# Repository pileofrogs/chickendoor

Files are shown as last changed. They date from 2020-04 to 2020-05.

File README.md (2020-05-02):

# chickendoor

We have chickens and live near Seattle where dawn is very early in the summers.
A system that opens the door to the chicken coop automatically means we can sleep in.  If it can also close the door, it makes vacations easier for a pet sitter.  

## Requirements

* Must fail safe:  IE if it breaks down, we can still open the door and latch it at night. - This is acheived by having the actuator outside of the chicken house and attached with simple pins that a person can pull out without tools
* Must be racoon proof:  Or you might as well not have a door
* Must not crush chickens:  This probably rarely happens, but I would feel aweful if it did.  I added a pressure sensor to make the door open if it hits anything.  
* Open and close based on sunrise & sunset:  No manual adjustmenst over the year.

## Files 

* openscad files for project box, pressure sensor & bracket
* openscad files for helpful objects (screw hole sizer, rpi mount position test)
* python code for running on Rpi

Requires a linear actuator, a set of 2 12v relays, a 12 & 5 v power supply, 
2 buttons && whatever I'm not remembering.

## How it works

The actuator is anchored on the wall outside of the door and to the door, so
when it retracts, it opens the door.  The pressure sensor is basically a hinge
connecting the actuator to the door with a button inside it.  When the actuator
presses on the hinge, it applies pressure to the button.  I just need to
position the button and possibly apply opposing elasic force.  

## TODO

* retry closing if we hit a chicken
* poweroff with long press
* log to syslog/journal
* send alerts if it hits a chicken or has other problems

## For version III

* config file for time offsets
* make brackets adjustable
* make it a service that I can interact with using a client
* make separate monitoring system that can send alerts if the chicken door opener dies
* figure out math for positioning the actuator
* separate latching mechanism
* camera and imge processing to count chickens
* anit-hawk rail-gun with tracking and flight prediction

## Lessons Leaned

* The slop between the pins and the holes they go through really matters.  Shutting the door firmly wihtout setting off the pressure sensor depends on minimal slop.  I was able to offset this by cramming some wire into the holes and screwing wood to the door, making it thicker.  
* setting one of the brackes a few inches off of the wall would really help.  As it is, the closed door is a straight line between them so there's very little leverage keeping it closed and that means any slop translates into a lot of wiggle in the door.
* gpiozero is amazing.  I could have written much simpler code if I'd known how   it works before I got started.

# pins I used

* LEDs 4,17 
* Relays 27,22
* Buttons 23,24

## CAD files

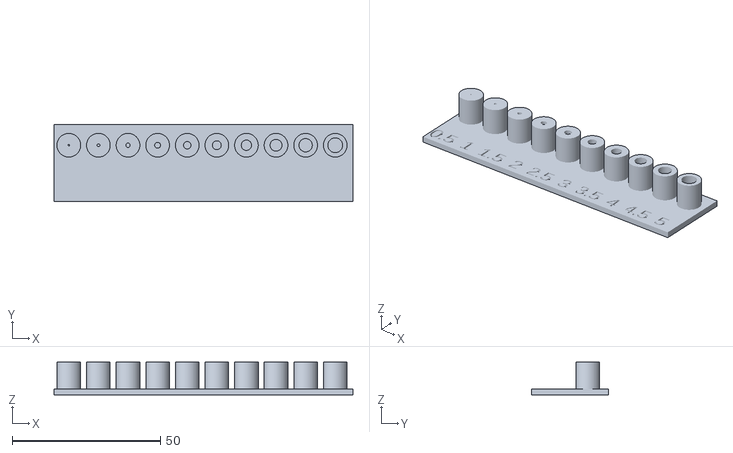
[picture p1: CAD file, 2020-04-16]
screw_hole_sizer.stl
101.0 x 26.0 x 11.0

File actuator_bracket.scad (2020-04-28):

act_r = 10.5;
act_hole_r = 3;
act_hole_d_to_end = 4;
act_hole_d_to_box = 8;
act_len = act_hole_d_to_end+act_hole_d_to_box+2*act_hole_r;
box = [39,39,39];
act_hole_shaft_len = 50;
clearance = 12; //
width = 5;
slop = 1;
upness = 30;

$fn = 100;

use <common_shapes.scad>;

echo(act_len);

module actuator () {
  hole_goes=act_hole_d_to_box+act_hole_r;
  translate([0,0,hole_goes]) rotate([0,90,0]) {
    translate([-box[0],-box[1]/2,-box[2]/2]) cube(box);
    difference() {
      rotate([0,90,0]) cylinder(act_len, act_r, act_r);
      translate([hole_goes, act_hole_shaft_len/2 , 0 ])
        rotate([90,0,0])
        cylinder( act_hole_shaft_len, act_hole_r, act_hole_r); 
    }
  }
}

module triangle (side,base) {
  hypot = sqrt(pow(side,2)+pow(base,2));
  angle = asin(base/hypot);
  difference () {
    cube([side,base,width]);
    translate([0,0,-1]) rotate([0,0,angle]) cube([hypot,base,width+2]);
  }
}

module ear () {
  translate ([0,0,clearance*2]) {
    rotate([-90,0,0]) {
      circler = act_hole_d_to_end+act_hole_r;
      difference () {
        union () {
          cylinder(width,circler,circler);
          translate([-circler,0,0]) cube([2*circler,2*clearance,width]);
          translate([-width/2,-circler+clearance,width]) 
            rotate([90,0,90])
            triangle(clearance+circler,clearance);
          translate([-circler,clearance,0]) rotate([0,0,90]) triangle(clearance,clearance/2);
          translate([circler,clearance,width]) rotate([180,0,90]) triangle(clearance,clearance/2);
        }
        translate([0,0,-1]) {
          cylinder(width+2,act_hole_r,act_hole_r);
        }
      }
    }
  }
}

translate([0,0,clearance*2]) %actuator();

translate([0,act_r+slop,0]) ear();
translate([0,-act_r-slop,0]) rotate([0,0,180])  ear();

ybase = 2*(clearance+width)+2*act_r+2*slop;
xbase = clearance+3*width;



difference() {
  translate([-xbase/2,-ybase/2,-width]) cube([xbase,ybase,width]);
  screw_head(3.5,4.1,2,width+slop);
  sx_offset = xbase/2-width;
  sy_offset = ybase/2-clearance/2;
  places = [
    [sx_offset,sy_offset,0],
    [-sx_offset,sy_offset,0],
    [sx_offset,-sy_offset,0],
    [-sx_offset,-sy_offset,0],
  ];
  for ( place = places ) {
    echo(place);
    translate(place) screw_head(3.5,4.1,2,width+slop);
  }
}

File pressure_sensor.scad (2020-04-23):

button = [6,3.5,3.5];

width = 5;
slop = 1;
pin_r = 2;

act_r = 10.5;
act_hole_r = 3;
act_len = 100;
act_hole_d_to_end = 6;
act_hole_shaft_len = 50;
hinge_plate_dims = [act_r*6, act_r*6, width];
barrel_r = width+pin_r;
wood_screw_radius = 2;
wood_screw_head_radius = 4.1;
wood_screw_head_height = 3.5;
wsr = wood_screw_radius;
wshr = wood_screw_head_radius;
wshh = wood_screw_head_height;

$fn = 100;

module actuator_piston () {
  hole_goes=-(act_hole_d_to_end+act_hole_r);
  %translate([hole_goes , 0, act_r]) {
    rotate([0,90,0]) cylinder(act_len, act_r, act_r);
    translate([-hole_goes, act_hole_shaft_len/2 , 0 ]) rotate([90,0,0]) cylinder( act_hole_shaft_len, act_hole_r, act_hole_r); 
  }
}

module ears ( thickness, rad, hole_rad ) {
  translate([0,rad,0]) difference() {
      union () {
          cylinder( thickness, rad, rad );
          translate([-rad*2,-rad,0]) cube([rad*4, rad, thickness]);
      }
      translate([0,0,-0.5]) cylinder( thickness+1, hole_rad, hole_rad);
      translate([ rad*2, 0, -0.5]) cylinder( thickness+1, rad,rad);
      translate([ -rad*2, 0, -0.5]) cylinder( thickness+1, rad,rad);
  }
}
translate([0,0,0.5*act_r]) actuator_piston();

module barrel_cut_out () {
    cylinder(hinge_plate_dims[0]/3+2*slop, barrel_r+slop, barrel_r+slop);
}

module hingetop () {
  // The flangy ear things around the piston
  translate([hinge_plate_dims[0]/2, hinge_plate_dims[1]/3-slop, 0]) rotate([90,0,0]) ears(width, 1.5 * act_r, act_hole_r);
  translate([hinge_plate_dims[0]/2, 2/3*hinge_plate_dims[1]+width+slop, 0]) rotate([90,0,0]) ears(width, 1.5 * act_r, act_hole_r);
  
  difference() {
    union () {
      // The hinge
      translate([0,0,-hinge_plate_dims[2]]) cube(hinge_plate_dims);
  
      // The barrel
      translate([hinge_plate_dims[0], 0, -barrel_r]) rotate([270, 0, 0]) 
      cylinder(hinge_plate_dims[0], barrel_r, barrel_r);
    }
    translate([hinge_plate_dims[0], 0, -barrel_r]) rotate([270, 0, 0]) {
      translate([0,0,-(slop/2)]) cylinder(hinge_plate_dims[0]+2,pin_r,pin_r);
      translate([0,0,-(slop/2)])  barrel_cut_out();
      translate([0,0, 2/3 * hinge_plate_dims[1]+slop])  barrel_cut_out();
    }
    // keeping it shut screw
    #translate([hinge_plate_dims[0]/6, hinge_plate_dims[1]/2, -wshh])
      screw_head();
  }

}

module hingebottom () {
  difference () {
    union () {
      translate([0,0, -hinge_plate_dims[2]]) cube(hinge_plate_dims);
      translate([0, 0, -barrel_r]) rotate([270, 0, 0]) 
        cylinder(hinge_plate_dims[0], barrel_r, barrel_r);
    }
    translate([0, 0, -barrel_r]) rotate([270, 0, 0]) {
      translate([0,0,-(slop/2)]) cylinder(hinge_plate_dims[0]+2,pin_r,pin_r);
      translate([0,0, hinge_plate_dims[1]/3+(slop/2)])  barrel_cut_out();
    }
    
    sixth = hinge_plate_dims[0]/6;
    screws_at = [ [barrel_r+sixth,sixth,0], 
                  [hinge_plate_dims[1]-sixth, sixth,0],
                  [hinge_plate_dims[1]-sixth, hinge_plate_dims[1]-sixth,0],
   		  [barrel_r+sixth,hinge_plate_dims[1]-sixth,0], 
    ];
    for ( screw_at = screws_at ) {
      translate(screw_at) rotate([180,0,0]) screw_head ();
    }
    // hole for keep-it-closed screw
    translate([hinge_plate_dims[0]-sixth, hinge_plate_dims[1]/2, -width-slop])
        cylinder(width+2*slop,wsr*1.5,wsr*1.5);
    // button trough
    trough_width = button[1]+2*slop;
    translate([-slop,hinge_plate_dims[1]/2-trough_width/2,-1.5*width])
      cube([hinge_plate_dims[0]+2*slop,button[1]+2*slop,width ]);
  }
}


translate([-hinge_plate_dims[0]/2,-hinge_plate_dims[1]/2,0]) hingetop();

translate([hinge_plate_dims[0]/2+barrel_r*2+2*slop,-hinge_plate_dims[1]/2,0]) hingebottom();

module screw_head () {
  overlap = wshh/100;
  translate([0,0,wshh-overlap]) cylinder(wshh,wshr,wshr);
  cylinder(wshh,wsr,wshr);
  translate([0,0,-wshh+slop]) cylinder(width+slop,wsr,wsr);
}

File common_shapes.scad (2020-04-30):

// wood_screw_head_height
// wood_screw_head_radius
// wood_screw_radius
// wood_screw_screw_height

module screw_head (wshh,wshr,wsr,wssh) {
  overlap = wshh/100;
  cylinder(1,wshr,wshr);
  translate([0,0,-wshh+overlap]) cylinder(wshh+overlap,wsr,wshr);
  translate([0,0,-wssh+overlap]) cylinder(wssh-wshh+overlap,wsr,wsr);
}

module standoff (height, rad, screw_rad) {
    difference () {
      cylinder(height, rad, rad);
      translate([0,0,rad-screw_rad]) cylinder(height, screw_rad, screw_rad);
    }   
}

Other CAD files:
project_box.scad
rpi_posts.scad
screw_hole_sizer.scad
standoffs.scad

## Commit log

2020-04-13 working on a project box
    [project_box.scad]
2020-04-16 screw hole sizer
    [project_box.scad, screw_hole_sizer.stl]
2020-04-16 working on the pressure sensor
    [pressure_sensor.scad, project_box.scad]
2020-04-17 simpler hinge
    [pressure_sensor.scad, project_box.scad]
2020-04-19 button & time
2020-04-19 behaviro around button seems right
2020-04-22 box looks ready, progress on pressure sensor
    [pressure_sensor.scad, project_box.scad]
2020-04-22 helpful stuff
    [rpi_posts.scad, screw_hole_sizer.scad]
2020-04-22 fixed after 1st print
    [project_box.scad]
2020-04-23 thingy to hold actuator to hen house
    [actuator_bracket.scad]
2020-04-23 pressure sensor done, starting bracket
    [pressure_sensor.scad]
2020-04-23 that shape wont work
    [actuator_bracket.scad]
2020-04-23 nice and sturdy
    [actuator_bracket.scad]
2020-04-28 all done with scad
    [actuator_bracket.scad, common_shapes.scad, project_box.scad]
2020-04-30 needed some free standoffs
    [standoffs.scad]
